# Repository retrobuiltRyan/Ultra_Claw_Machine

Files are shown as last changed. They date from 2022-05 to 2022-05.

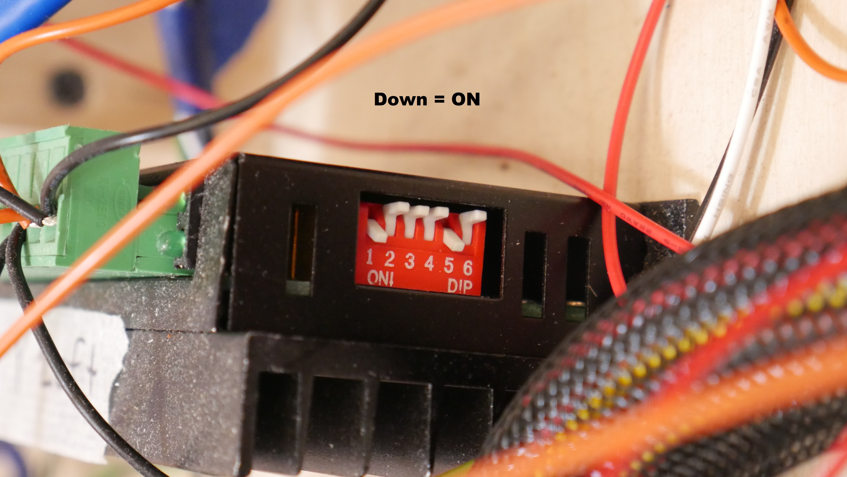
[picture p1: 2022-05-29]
MicroStepping Switch Positions.JPG

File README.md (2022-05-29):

# Ultra_Claw_Machine
A full size (68 x 36 x 31inch) Arduino Mega based claw machine. Borrows most of its design characteristics from DIY CNC machines and 3D printers.
Please watch the Youtube video https://youtu.be/VPqZMdIZ9Dg for a general overview of the design and construction. Happy building!

P1040743
Claw Machn ELECTRICAL Diagram
CAD ariel overview

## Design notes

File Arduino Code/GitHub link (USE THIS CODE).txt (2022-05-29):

https://github.com/LupeCarlos/CMU-TechSpark-Claw-Machine

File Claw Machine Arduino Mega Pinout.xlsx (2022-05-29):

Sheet: Sheet1
CLAW MACHINE PINOUT |  | May 24 2022 | Arduino MEGA
 | OUTPUT | Pin# | Notes
 | X Step (Pul+) | 11
 | X Direction | 10
 | Y1 Step (Pul+) | 9
 | Y1 Direction | 8
 | Y2 Step (Pul+) | 7
 | Y2 Direction | 6 | (mirror of Y1)
 | Z Claw Step (Pul+) | 13
 | Z Claw Direction | 12
 | X Min | 15
 | X Max | 14
 | Y Min | 3
 | Y Max | 2
 | Z Claw Limit | 4
 | LCD i2c | 20 | SDA (cannot be changed)
 | LCD i2c | 21 | SCL (cannot be changed)
 | ClawServo Relay Power | 53
 | Stepper Enable | 52 | Wired to all steppers. LOW = Enable
 | Adressable LED Data | TBD | not implimented yet
 | Claw / Servo PWM | 5
 | INPUT (user controls) | Pin# | Notes
 | Forward (joystick) | 22
 | Backward (joystick) | 23
 | Left (joystick) | 24
 | Right (joystick) | 25
 | Up (button) | 26
 | Down (button) | 27
 | Close (button) | 28
 | Open (button) | 29
 | Start (button) | 30
 | Coin Slot (button) | 31
 | Game Mode (switch) | 16
 | Game Timer Potentiometer | A12
 | Servo Wiring is
 | Orange = GND
 | White = Com
 | Red = +5V

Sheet: ToDo
CLAW MACHINE To Do REV ? |  |  | Arduino MEGA
 | CODE / Electrical | Pin# | Notes
 | Move Motors
 | Mechanical | Pin# | Notes
 | Add master Input Power connector
 | Strain Releif

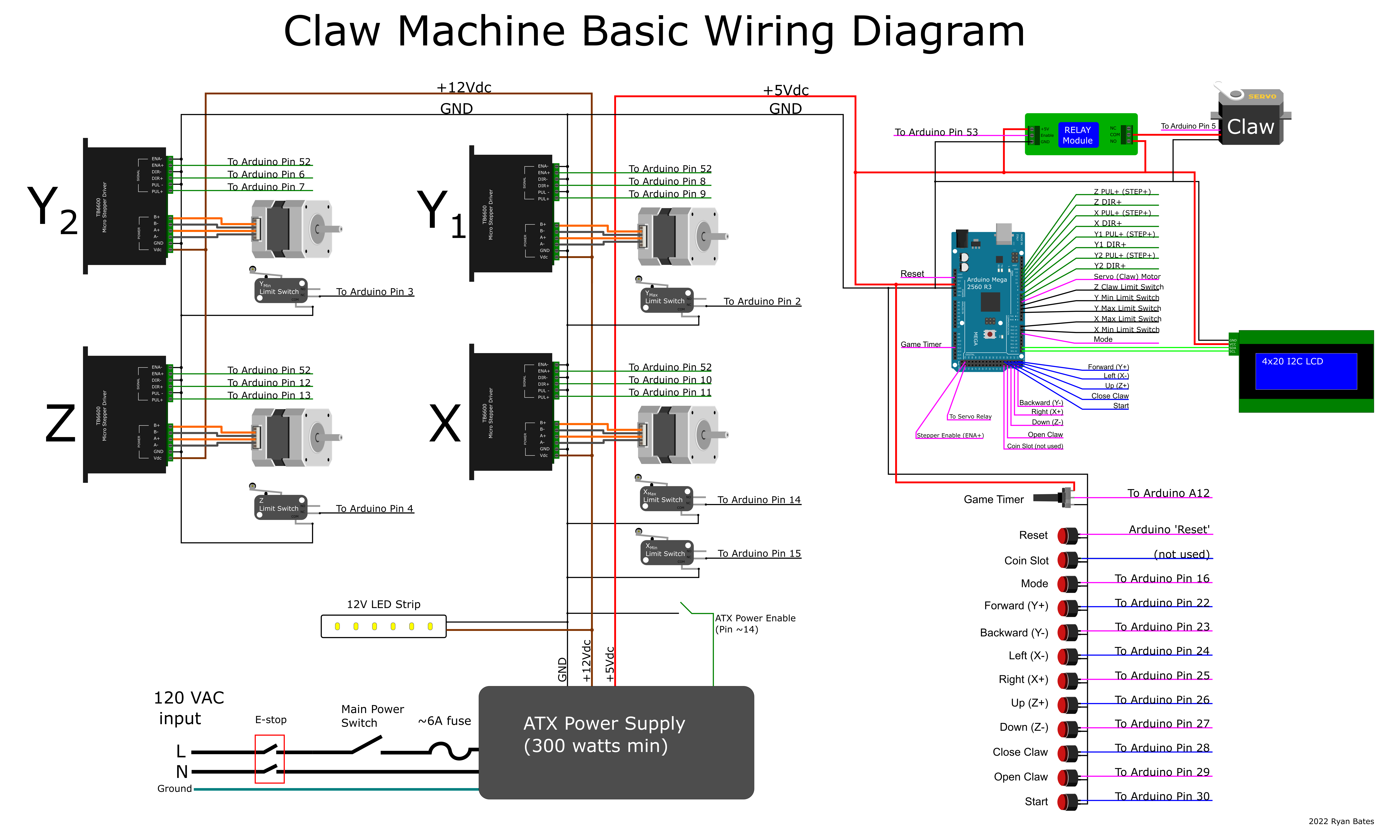
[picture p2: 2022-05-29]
Claw Machn ELECTRICAL Diagram.png

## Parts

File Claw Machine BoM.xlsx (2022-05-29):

Category | Item | Description | Quantity | Cost |  | Line Total
Body | 1 | 3/4 inch Furniture Grade Plywood 8x4 ft sheet | 5 | $73.00 |  | $365.00
 | 2 | Acrylic sheet 0.125in 24x48inch sheet | 3 | $25.00 |  | $75.00
 | 3 | T-molding 3/4inch wide, black (1Ft) | 30 | $0.50 |  | $15.00
 | 4 | Paint + Primer (1 quart each should cover it?) | 1 | $24.00 |  | $24.00
User control | 5 | Arcade Joystick (8-way) | 1 | $16.00 |  | $16.00
 | 6 | Arcade Push Buttons (1.125") | 5 | $2.00 |  | $10.00
 | 7 | Misc Switches, potentiometers, small push buttons | 1 | $7.00 |  | $7.00
Mechanical | 8 | NEMA 23 Stepper Motor | 4 | $30.00 |  | $120.00
 | 9 | Servo Motor | 1 | $10.00 |  | $10.00
 | 10 | Aluminum 1x1 Ft (0.25in thick) 6061 | 2 | $35.00 |  | $70.00
 | 11 | Aluminum Extrusion 1x1inch (3ft section) | 4 | $16.65 | https://www.mcmaster.com/47065T101-47065T412/ | $66.60
 | 12 | Aluminum Extrusion 2x1inch (3ft section) | 1 | $26.00 | https://www.mcmaster.com/47065T107-47065T419/ | $26.00
 | 13 | Aluminum Extrsusion 90degree Brackets | 16 | $7.92 | https://www.mcmaster.com/47065T236/ | $126.72
 | 14 | Hardboard 0.25inch thick 1x1 Ft | 1 | $2.00 |  | $2.00
 | 15 | Cable Carrier | 2 | $18.00 |  | $36.00
 | 16 | lots of misc nut bolt hardware | 1 | $20.00 |  | $20.00
Electrical | 17 | Arduino Mega | 1 | $15.00 |  | $15.00
 | 18 | Arduino Mega Screw Terminal Shield | 1 | $24.00 |  | $24.00
 | 19 | Microswitch | 5 | $1.50 |  | $7.50
 | 20 | Stepper Driver (TB6600) | 4 | $15.00 |  | $60.00
 | 21 | LED lights 12V 1ft White strip | 18 | $2.00 |  | $36.00
 | 22 | Aluminum mounting channel for LED strips, 3m | 1 | $27.00 |  | $27.00
 | 23 | IEC socket with Switch (Fuse Required) | 1 | $4.00 |  | $4.00
 | 24 | Fuse | 1 | $1.00 |  | $1.00
 | 25 | RJ45 Breakout PCB (with RJ45 socket) | 6 | $1.50 |  | $9.00
 | 26 | lots of wires | 99 | $0.25 |  | $24.75
Specialty hardware | 27 | Binding Posts (low profile) Aluminum 8-32 x 0.5inch (pack of 25) | 2 | $16.50 | https://www.mcmaster.com/93121A335/ | $33.00 | black annodized https://www.mcmaster.com/99024A334/
 | 28 | Butteryfly latches | 4 | $3.00 |  | $12.00
 | 29 | Caster wheels if you want to move it | 4 | $6.00 |  | $24.00
 |  |  |  |  |  | $1266.57
 |  | Raw Cost | 1242
 |  | Thrifty build | 567

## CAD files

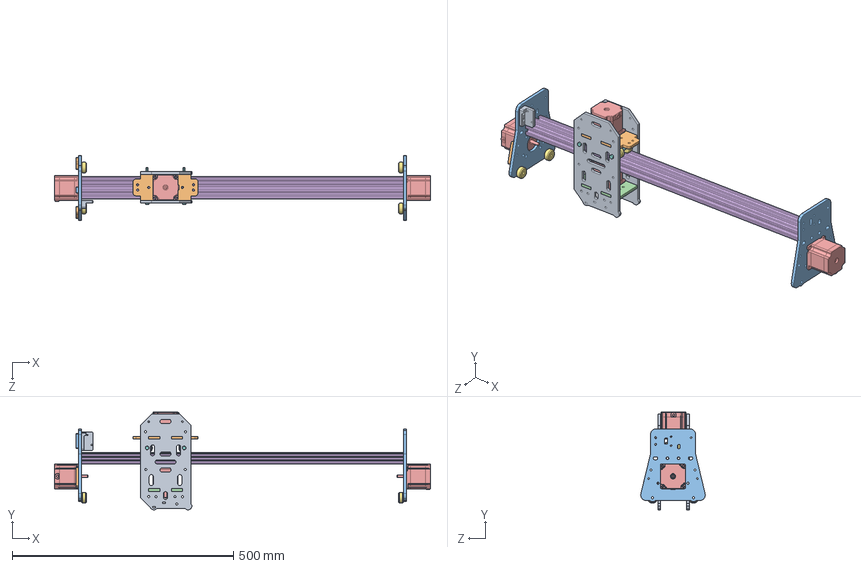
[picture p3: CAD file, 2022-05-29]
Solidworks ClawMachine CAD/Gantry Parts/XYZ Gantry.SLDASM
849.1 x 220.8 x 145.8 mm
Gantry Plate X x 2
Gantry Plate X2
Gantry Plate Y x 2
Gantry Plate Z
Stepper Motor (GrabCAD) x 4
47065T213_T-Slotted Framing
Ilder Wheel x 8
91280A264_Medium-Strength Class 8.8 Steel Hex Head Screw x 2
X Gantry Limit Switch Holder
Y Limit Switch bumper x 2
X Belt Clip

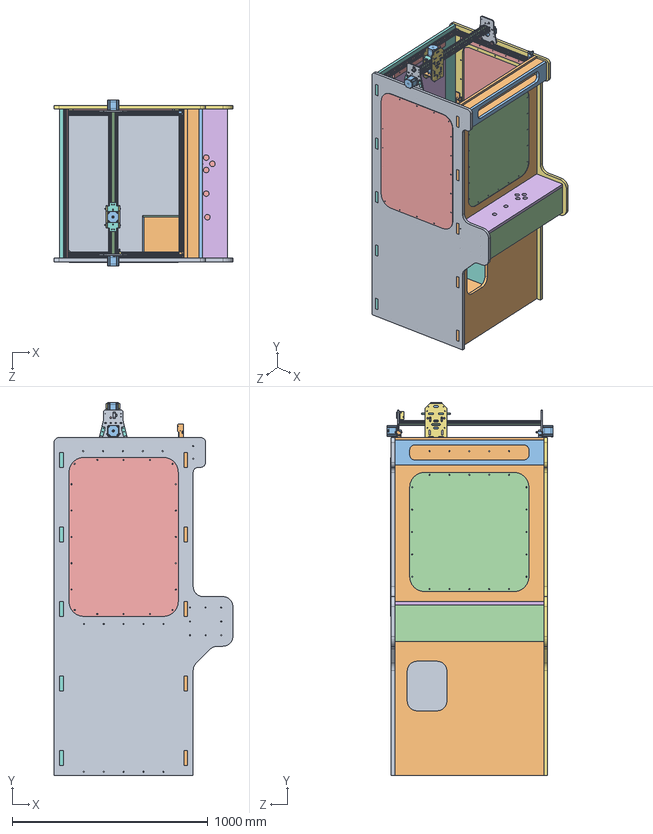
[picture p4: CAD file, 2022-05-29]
Solidworks ClawMachine CAD/Claw Machine.SLDASM
914.4 x 1906.3 x 849.1 mm
Side Panel Body
Front Panel Body
ctrlpanel_side x 2
ctrlpanel_front
ctrlpanel_bottom
ctrlpanel_top
Side Panel Body_right
Back Panel Body
prizefloor
marquee_top x 2
marquee_front
marquee_side x 2
Shelf support bracket 20in x 10
Shelf support bracket 5in
Floor bottom
Prize Chute Right
Prize Chute Rear
Prize Chute Bottom
Prize Floor Barrier A
Prize Floor Barrier B
47065T411_T-Slotted Framing 30in x 2
47065T411_T-Slotted Framing 22.5in x 2
Gantry Plate X x 2
Gantry Plate X2
Gantry Plate Y x 2
Gantry Plate Z
Stepper Motor (GrabCAD) x 4
47065T213_T-Slotted Framing
Ilder Wheel x 8
91280A264_Medium-Strength Class 8.8 Steel Hex Head Screw x 2
X Gantry Limit Switch Holder
Y Limit Switch bumper x 2
X Belt Clip
Y Gantry Limit Switch Holder
Y Gantry Belt Holder
Front Panel Window
Side Panel Window x 2

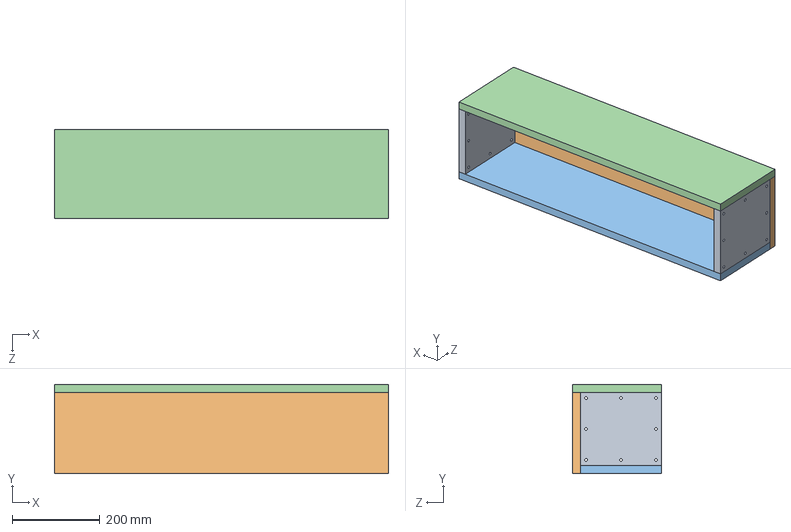
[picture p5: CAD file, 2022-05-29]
Solidworks ClawMachine CAD/ctrlpanel_assem.SLDASM
762.0 x 203.2 x 203.2 mm
ctrlpanel_side x 2
ctrlpanel_front
ctrlpanel_bottom
ctrlpanel_top

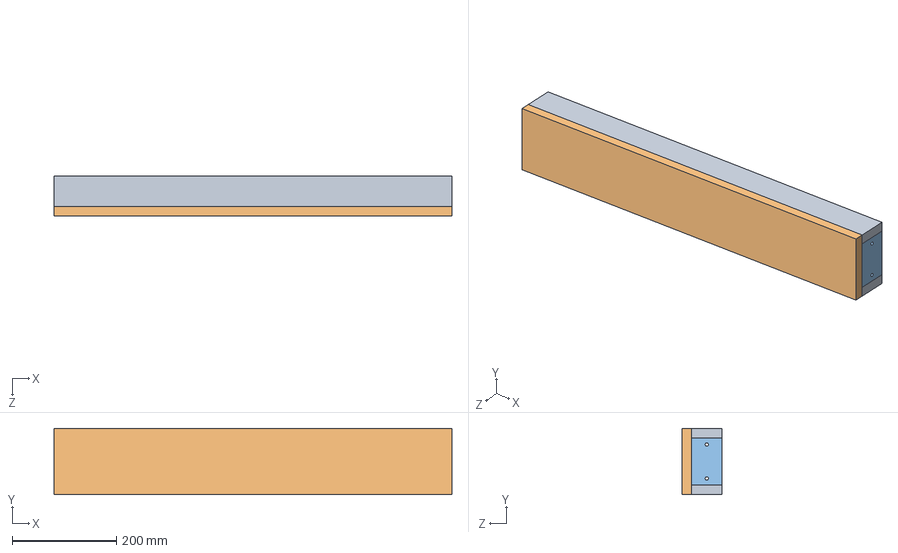
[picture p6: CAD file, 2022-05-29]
Solidworks ClawMachine CAD/marquee_assem.SLDASM
762.0 x 127.0 x 76.2 mm
marquee_top x 2
marquee_front
marquee_side x 2

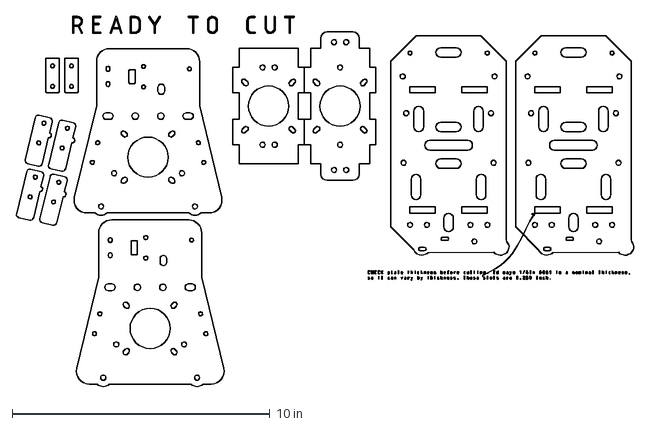
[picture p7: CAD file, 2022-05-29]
Solidworks ClawMachine CAD/Gantry Parts/waterjet claw machine gantry plates.dxf
24.0 x 14.4 in

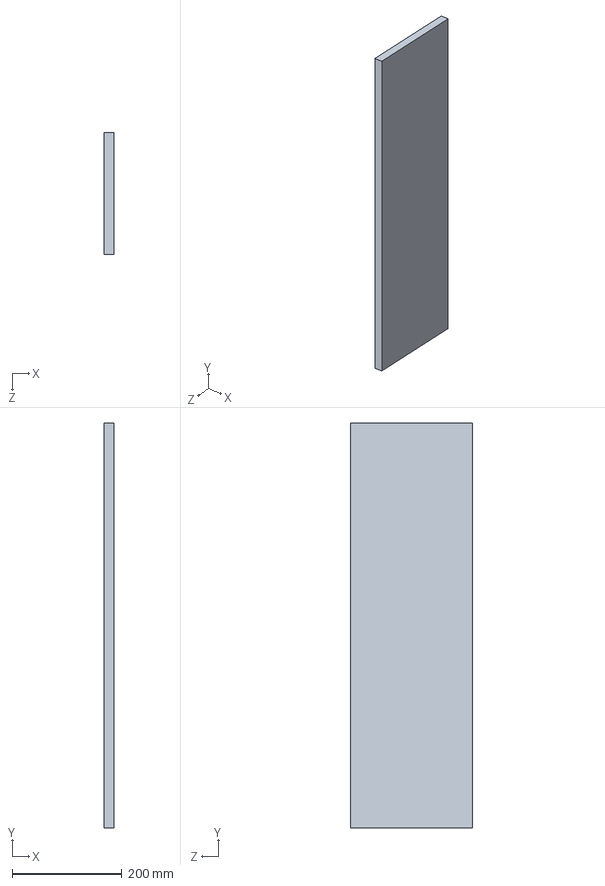
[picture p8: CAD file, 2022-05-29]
Solidworks ClawMachine CAD/Prize Chute Right.SLDPRT
18.3 x 736.6 x 222.2 mm

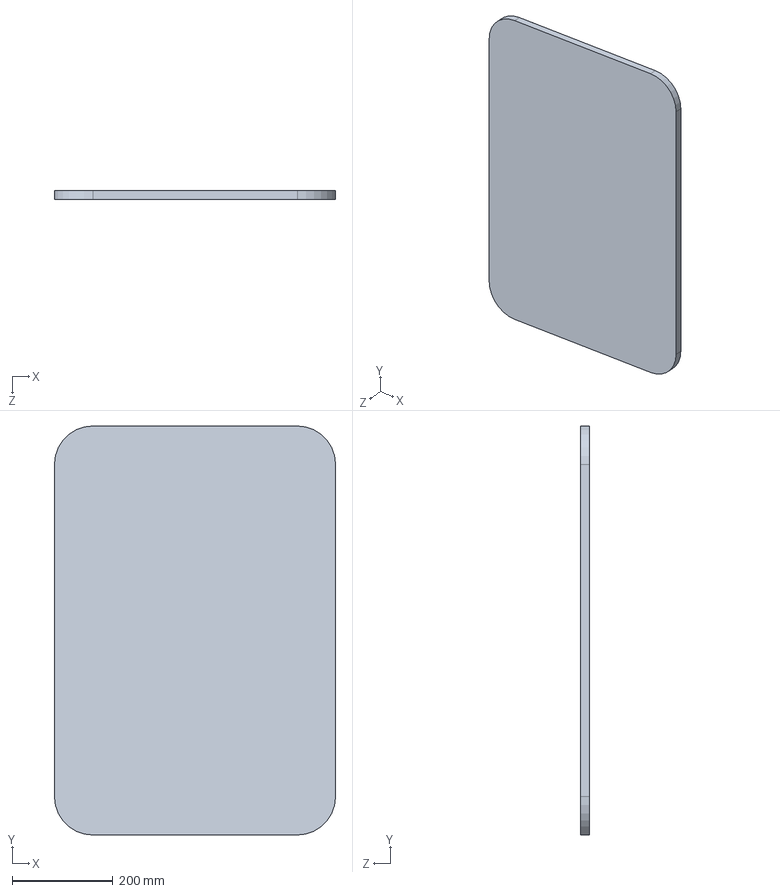
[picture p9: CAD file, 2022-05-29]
Solidworks ClawMachine CAD/Back Panel Removeable Door.SLDPRT
558.8 x 812.8 x 18.3 mm

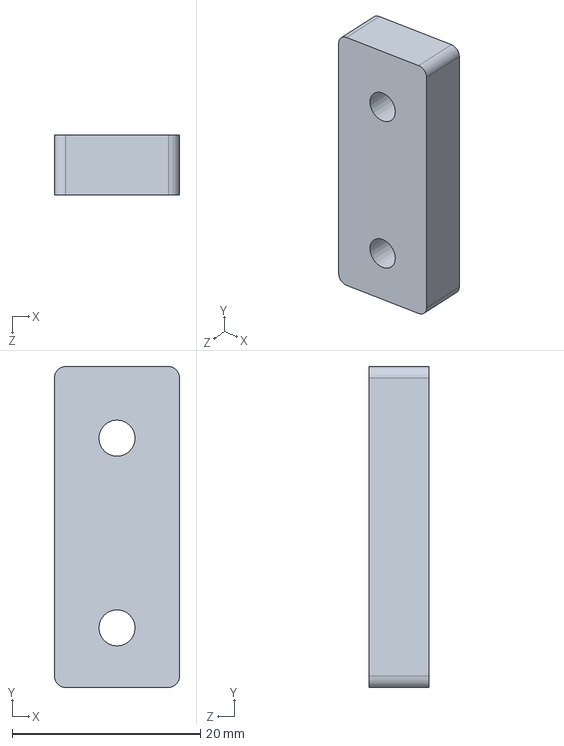
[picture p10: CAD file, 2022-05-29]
Solidworks ClawMachine CAD/Gantry Parts/X Belt Clip.SLDPRT
13.3 x 34.1 x 6.35 mm

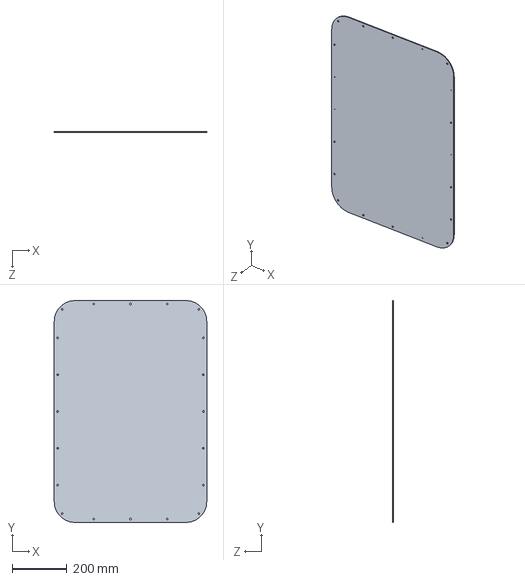
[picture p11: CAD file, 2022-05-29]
Solidworks ClawMachine CAD/Side Panel Window.SLDPRT
558.8 x 812.8 x 3.17 mm

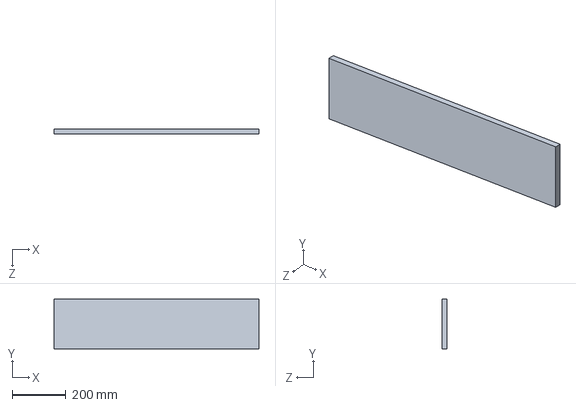
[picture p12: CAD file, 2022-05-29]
Solidworks ClawMachine CAD/ctrlpanel_bottom.SLDPRT
762.0 x 184.9 x 18.3 mm

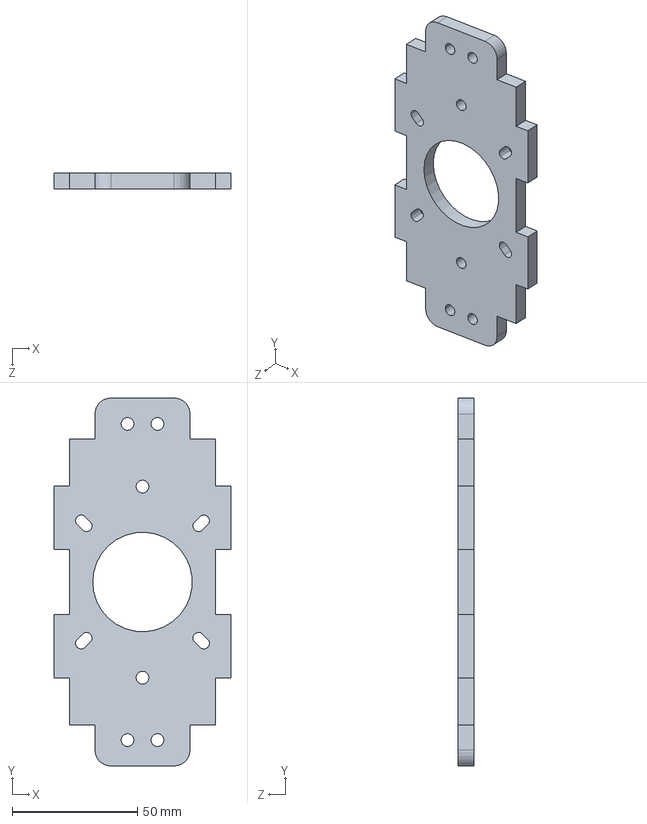
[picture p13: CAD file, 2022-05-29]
Solidworks ClawMachine CAD/Gantry Parts/Gantry Plate X2.SLDPRT
70.5 x 146.7 x 6.35 mm

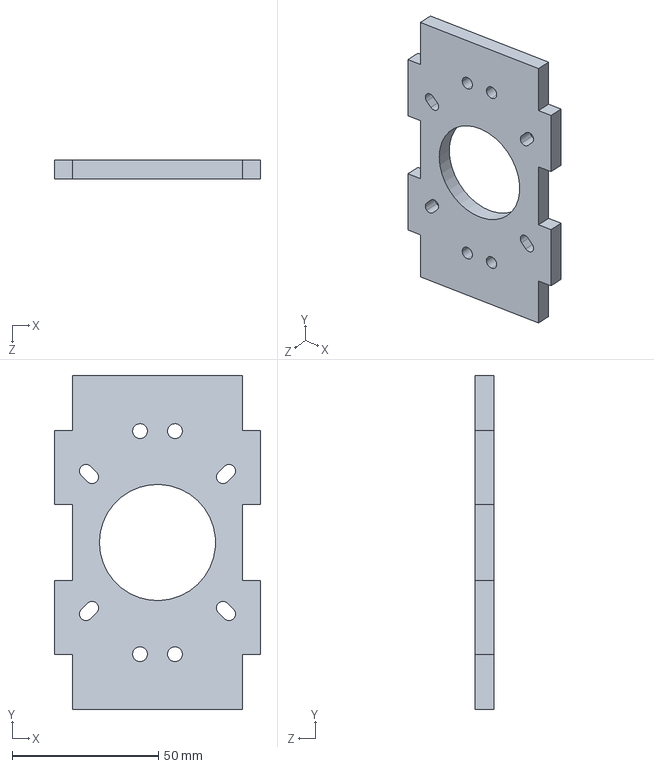
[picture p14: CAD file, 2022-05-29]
Solidworks ClawMachine CAD/Gantry Parts/Gantry Plate Z.SLDPRT
70.5 x 114.1 x 6.35 mm

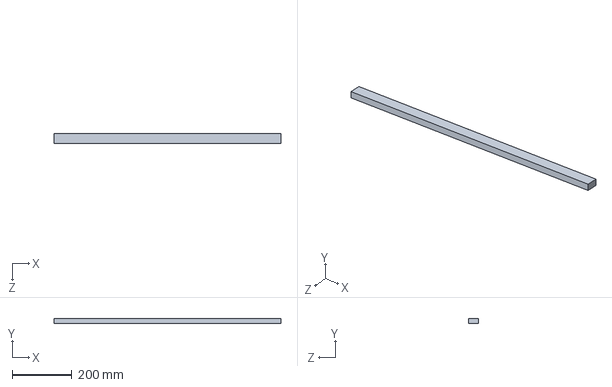
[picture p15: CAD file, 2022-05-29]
Solidworks ClawMachine CAD/marquee_top.SLDPRT
762.0 x 18.3 x 32.5 mm

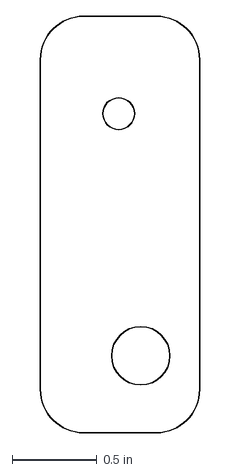
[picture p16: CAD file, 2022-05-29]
Solidworks ClawMachine CAD/bumper for limit switch.dxf
0.942 x 2.46 in

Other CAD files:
Solidworks ClawMachine CAD/Gantry Parts/Ilder Wheel.SLDPRT
Solidworks ClawMachine CAD/Gantry Parts/Y Limit Switch bumper.SLDPRT
Solidworks ClawMachine CAD/RJ45 bracket holder thing.STL
Solidworks ClawMachine CAD/Back Panel Body.SLDPRT
Solidworks ClawMachine CAD/47065T411_T-Slotted Framing 22.5in.SLDPRT
Solidworks ClawMachine CAD/47065T411_T-Slotted Framing 30in.SLDPRT
Solidworks ClawMachine CAD/Back Panel Removable Door.DXF
Solidworks ClawMachine CAD/Floor bottom.SLDPRT
Solidworks ClawMachine CAD/Front Panel Body.SLDPRT
Solidworks ClawMachine CAD/Front Panel Window.DXF
Solidworks ClawMachine CAD/Front Panel Window.SLDPRT
Solidworks ClawMachine CAD/Gantry Parts/47065T213_T-Slotted Framing.SLDPRT
Solidworks ClawMachine CAD/Gantry Parts/91280A264_Medium-Strength Class 8.8 Steel Hex Head Screw.SLDPRT
Solidworks ClawMachine CAD/Gantry Parts/Gantry Plate X.SLDPRT
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

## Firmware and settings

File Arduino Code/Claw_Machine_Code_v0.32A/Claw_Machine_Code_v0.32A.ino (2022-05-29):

// Ryan Bates || Brian Lee
// TechSpark Claw Machine + Accel Stepper Motors
// Sept 29 2021

/* ============Ryan's Change Log [Add new features]:=================
 * Start button, Coin Insert button; triggers game start and game cycles
 * Gameplay loop, 60 second timers 
 * 4x20 i2C LCD to give user feedback and debug
 * [On going] LCD and LED updates are only once per 1 second
 * [On going] Swapped in sub routines to make code more readable
 * [On going] Addressable LEDs change color based on what is happening (idle, in game-timer, gameover)
 * 
 * [Have Not Added] homing functions for  1) power on and 2) gameOver
 * [Have Not Added] Test mode (full control without timer and LCD read what inputs are pressed.)
 * [On going] Serial Monitor debug (print what is happening all the time) will eventually comment out all of this to save processor resources. 
 * [Have Not Added] Demo Mode (press button (secret location) for a random x,y, position and claw grab. 
 * [Have Not Added] Luck/ Mode to toggle between.
 * [Have Not Added] Enable/ Diable Stepper moters & Claw when idle. ENA pin needs to be wired and pulled LOW to cut motor
   power when not in use (Claw Machine is in idle).ENA+ (+5v) ENA- (to arduino) i think this is right? 
 * [Might Change/ Refine] Servo / Claw behavior

i am ass at programming. Sincerely, Ryan
*/
#include <Servo.h>
#include <Stepper.h>
#include <Adafruit_NeoPixel.h> // for addressable RGB LEDs
#define PIN            16 //pin on the Arduino is connected to the NeoPixels?
#define NUMPIXELS      12 // How many NeoPixels are attached to the Arduino?
Adafruit_NeoPixel pixels = Adafruit_NeoPixel(NUMPIXELS, PIN, NEO_GRB + NEO_KHZ800);

#include <Wire.h> 
#include <LiquidCrystal_I2C.h>
LiquidCrystal_I2C lcd(0x27,20,4);  // set the LCD address to 0x27 (address can vary) for a 20 chars and 4 line display

Servo claw;
const int clawPin = 5;
const int clawUp = 26;
const int clawDown = 27;
const int clawClose = 28;
const int clawOpen = 29;
const int startButton = 30;
const int coinInsert= 31; 
const int servoRelay = 53;
const int StepperEnable = 52; /// NEW!
const int stepperSpeedDelay = 1;
const int stepperPulse = 1;

int clawStep = 15; // degrees
int clawCurValue = constrain(clawCurValue, 0, 180);
int clawOpenButtonState = 0;
int clawOpenButtonLastState = 0;
int clawCloseButtonState = 0;
int clawCloseButtonLastState = 0;

const int xStepPin = 11; 
const int xDirPin = 10;
const int y1StepPin = 9;
const int y1DirPin = 8;
const int y2StepPin = 7;
const int y2DirPin = 6;

const int zStepPin = 13;  //(claw up/down)
const int zDirPin = 12;   //(claw up/down)

const int xMinLmtSwtch = 15;
const int xMaxLmtSwtch = 14;
const int yMinLmtSwtch = 3;
const int yMaxLmtSwtch = 2;
const int clawLmtSwtch = 4;

const int forwardJoystick = 22;
const int backwardJoystick = 23;
const int leftJoystick = 24;
const int rightJoystick = 25;

const int stepsPerRevolution = 200;  // change this to fit the number of steps per revolution
//Stepper Xstepper(stepsPerRevolution, 11,11); // library wants 2 or 4 wires (pins) to send pulses too, but these stepper
//Stepper Y1stepper(stepsPerRevolution, 9,9); //  drivers (TB6600?) only step and direction pin to interface. 
//Stepper Y2stepper(stepsPerRevolution, 7,7); //  What i am saying is, this will compile ok, just pay no mind to it. 
//Stepper Zstepper(stepsPerRevolution, 13,13); // 

//------------------time keeping variables for the gameplay loop------------------------------------

//unsigned long previousMillis = 0;            // timestamp made when something happens; dont think this is used anymore.
const long gameloopTimeLimit = 20;             // Game play Time Limit. Time that clawmachine will respond to user input
long elapsedTime;                              // Elasped game time in seconds (counts up!) 
long countDown;                                // Remaining game time in seconds, (counts down!)

unsigned long seconds;
unsigned long gameStartTime;

// ------------------time keeping variables for updating the LCD and LED strips once every so often------------------
unsigned long previousMillis1 = 0;        // will store last time LED was updated
const long updateInterval = 1000;         // interval at which to update user visual feedback

void setup() {
  pinMode(xStepPin, OUTPUT);
  pinMode(xDirPin, OUTPUT);
  pinMode(y1StepPin, OUTPUT);
  pinMode(y1DirPin, OUTPUT);
  pinMode(y2StepPin, OUTPUT);
  pinMode(y2DirPin, OUTPUT);
  pinMode(zStepPin, OUTPUT);
  pinMode(zDirPin, OUTPUT);
  pinMode(servoRelay, OUTPUT);
  pinMode(StepperEnable, OUTPUT);
    
  pinMode(xMinLmtSwtch, INPUT_PULLUP);
  pinMode(xMaxLmtSwtch, INPUT_PULLUP);
  pinMode(yMinLmtSwtch, INPUT_PULLUP);
  pinMode(yMaxLmtSwtch, INPUT_PULLUP);
  pinMode(clawLmtSwtch, INPUT_PULLUP);

  pinMode(clawUp, INPUT_PULLUP);
  pinMode(clawDown, INPUT_PULLUP);
  pinMode(clawOpen, INPUT_PULLUP);
  pinMode(clawClose, INPUT_PULLUP);
  pinMode(forwardJoystick, INPUT_PULLUP);
  pinMode(backwardJoystick, INPUT_PULLUP);
  pinMode(leftJoystick, INPUT_PULLUP);
  pinMode(rightJoystick, INPUT_PULLUP);
  pinMode(startButton, INPUT_PULLUP);


//Xstepper.setSpeed(400);
//Y1stepper.setSpeed(200);
//Y2stepper.setSpeed(200);
//Zstepper.setSpeed(400);
  claw.attach(clawPin); //attaches servo to PWN pin
  pixels.begin();       // This initializes the NeoPixel library.
  
  Serial.begin(9600);   // initialize the serial port:
  
  lcd.init();      //initialize the LCD
  lcd.backlight(); //turn on backlight
  lcd.setCursor(5,0);
  lcd.print("TechSpark's");
  lcd.setCursor(4,1);
  lcd.print("Ultra Claw");
  delay(1000);
  lcd.clear();
}

void loop() {//+++++++++++START OF LOOP+++++++++++++++++++++++++
lcd.setCursor(0,0);
lcd.print("Press Start to play!");
digitalWrite(StepperEnable, HIGH);     // disable motors at the motor driver (EN+)
Serial.println("Press Start to play!");
unsigned long seconds = millis()/1000; // mark the system time as currentmillis
  
  //lcd.setCursor(0,1);   //this is debug, showing the Arduino system time
  //lcd.print("System time: ");lcd.print(seconds); 

  
while (digitalRead(startButton)==LOW){ //enter this loop only when the start button is pressed
      runGameSkill();
  }

 
}  //---------------END OF LOOP---------------------------------



void runGameSkill(){
  lcd.clear();
  digitalWrite(StepperEnable, LOW);     // Enaable motors at the motor driver (EN+)
   digitalWrite(servoRelay, HIGH); // enable power to the servo (claw)
   for(int i=0;i<NUMPIXELS;i++){
    // pixels.Color takes RGB values, from 0,0,0 up to 255,255,255
    pixels.setPixelColor(i, pixels.Color(0,10,0)); // Moderately bright green color.
    pixels.show(); // This sends the updated pixel color to the hardware.
    lcd.setCursor(0,3); lcd.print("elapsed Time: ");
    delay(5); // Delay for a period of time (in milliseconds).
   }
   
  //===========Time Keeping Functions=====MUCH IMPORTANT, NO TOUCH==================================
  gameStartTime = millis()/1000; //mark the system time as 'now'.
while (millis()/1000 - gameStartTime < gameloopTimeLimit){
  elapsedTime = millis()/1000- gameStartTime; // subtract system clock time from the "now" time stamp
  lcd.print(elapsedTime); // using this variable to light LEDs with Game time
  lcd.print("    ");
  LCD_LED_update(); //updates screen and shows some visual feedback for game timer



     
//==================Enable MOVEMENT======================================================
// Movement must be written as while loops. The controls must have program priority so they under inputs feel responsive.
// In the background of each loop time is being checked to force gameover if stuck in movement loop.

  while ((digitalRead(leftJoystick) == LOW) && (digitalRead(xMinLmtSwtch) == HIGH) ){
    countDown = gameStartTime+gameloopTimeLimit-millis()/1000; // this force breaks the loop if the time expires
    if (countDown== 0)
    {break;}
    X_left();  
      LCD_LED_update();  

    }
    
  while ((digitalRead(rightJoystick) == LOW) && (digitalRead(xMaxLmtSwtch) == HIGH)){
    countDown = gameStartTime+gameloopTimeLimit-millis()/1000;
    if (countDown== 0)
    {break;}
   X_right();
     LCD_LED_update();    
   
   }

  while ((digitalRead(forwardJoystick) == LOW) && (digitalRead(yMaxLmtSwtch) == HIGH)) {
    countDown = gameStartTime+gameloopTimeLimit-millis()/1000; // this force breaks the loop if the time expires
    if (countDown== 0)
    {break;}
  Y_forward(); 
    LCD_LED_update();
  
  }
  
  while ((digitalRead(backwardJoystick) == LOW) && (digitalRead(yMinLmtSwtch) == HIGH)){
    countDown = gameStartTime+gameloopTimeLimit-millis()/1000; // this force breaks the loop if the time expires
    if (countDown== 0)
    {break;}
  Y_backward(); 
    LCD_LED_update();
  }

  
  while ((digitalRead(clawUp) == LOW) && (digitalRead(clawLmtSwtch) == HIGH)){
  countDown = gameStartTime+gameloopTimeLimit-millis()/1000; // this force breaks the loop if the time expires
    if (countDown== 0)
    {break;}
  Zclaw_up(); 
    LCD_LED_update(); 
  }

  while ((digitalRead(clawDown) == LOW)){
   countDown = gameStartTime+gameloopTimeLimit-millis()/1000; // this force breaks the loop if the time expires
    if (countDown== 0)
    {break;} 
  Zclaw_down();
    LCD_LED_update();
  }

 clawOpenServo();
 clawCloseServo();

}
gameOver();
returnHome();

}
void LCD_LED_update()                                       {
  unsigned long currentMillis1 = millis();          // does this go here? maybe higher up in the loop
    if (currentMillis1 - previousMillis1 >= updateInterval) {
    // save the last time you updated the status
    previousMillis1 = currentMillis1;
    // do the thing once per interval
     //-----countdown timer and bar animation
     lcd.setCursor(17,1); 
     countDown = gameStartTime+gameloopTimeLimit-millis()/1000; // count down Timer
     lcd.print(countDown); // show the count down seconds so you know the game will end
     if ((gameStartTime+gameloopTimeLimit-millis()/1000) < 10)
     lcd.print(" "); //fixes the missing leading zero for numbers under 10
     lcd.setCursor(4,1); lcd.print("Time Limit:");
     lcd.setCursor((millis()/1000- gameStartTime)*1,2); lcd.write(0xFF); //LCD status bar for time 
     //-----some LED + visual feedback based on how much time is left
    pixels.setPixelColor(countDown, pixels.Color(10,0,0)); //red color.
    pixels.show();
    }}
//void displayTime(){ //obsolete, rolled into the update LED and LCD routine
// //-----countdown timer and bar animation
//     lcd.setCursor(17,1); 
//     countDown = gameStartTime+gameloopTimeLimit-millis()/1000; // count down Timer
//     lcd.print(countDown); // show the count down seconds so you know the game will end
//     if ((gameStartTime+gameloopTimeLimit-millis()/1000) < 10)
//     lcd.print(" "); //fixes the missing leading zero for numbers under 10
//     lcd.setCursor(4,1); lcd.print("Time Limit:");
//     lcd.setCursor((millis()/1000- gameStartTime)*1,2); lcd.write(0xFF); //LCD status bar for time
//  
//}
void returnHome(){
 // code to home machine to prize shoot (x0,y0,z0) 
 // Close claw | wait a second | Goto Z0
 // Lift claw to Z min switch
  while (digitalRead(xMinLmtSwtch) == HIGH)
  X_left();
  while (digitalRead(yMinLmtSwtch) == HIGH)
  Y_forward();
 // Open claw

 // Turn off LEDs
    lcd.clear(); lcd.setCursor(0,0);
    LEDS_off();
}

void gameOver(){
   lcd.clear(); lcd.setCursor(0,0);
    for(int i=0;i<3;i++){ //Blink LEDs on/off red for GAMEOVER
      colorWipe(pixels.Color(0, 0, 0), 0); // Red
      delay(250); // Delay for a period of time (in milliseconds).
      colorWipe(pixels.Color(10, 0, 0), 0); // Red
      delay(250); // Delay for a period of time (in milliseconds).
    }
   lcd.print("GAME OVER!");  // could animate this to stall for time? 
   for (int i=0; i<= 4; i++){
     lcd.print(" GAME OVER!    ");  // could animate this to stall for time? 
     delay(200);            }
   delay(100);
   lcd.clear(); lcd.setCursor(4,1);
    digitalWrite(servoRelay, LOW); //disable power to the servo (claw)
 }
void LEDS_off(){
    for(int i=0;i<NUMPIXELS;i++){ //turn LEDs RED for GAMEOVER
    // pixels.Color takes RGB values, from 0,0,0 up to 255,255,255
    pixels.setPixelColor(i, pixels.Color(0,0,0)); // Turn off.
    pixels.show(); 
    delay(100); // Delay for a period of time (in milliseconds).
    }
}

void colorWipe(uint32_t c, uint8_t wait) {
  for(uint16_t i=0; i<pixels.numPixels(); i++) {
    pixels.setPixelColor(i, c);
    pixels.show();
    delay(0);
  }
}

//==================Gantry Movement subroutines=======Please Keep things tidy=======================
/*
Stepper Xstepper(stepsPerRevolution, 11,11); // library wants 2 or 4 wires (pins) to send pulses too, but these stepper
Stepper Y1stepper(stepsPerRevolution, 7,7); //  drivers TB6600? only step and direction pin to interface. 
Stepper Y2stepper(stepsPerRevolution, 9,9); //  What i am saying is this will compile ok, just pay no mind to it. 
Stepper Zstepper(stepsPerRevolution, 13,13); // 

 */
void X_left(){
  digitalWrite(xDirPin, LOW);   //left direction
  digitalWrite(xStepPin, HIGH); 
  delay(stepperPulse);
  digitalWrite(xStepPin, LOW); 
  delay(stepperPulse);        // speed 
  //Serial.println("Left");
}

void X_right(){
  digitalWrite(xDirPin, HIGH);   //right direction
  digitalWrite(xStepPin, HIGH); 
  delay(stepperPulse);
  digitalWrite(xStepPin, LOW); 
  delay(stepperPulse);        // speed 
 // Xstepper.step(25);
  //Serial.println("Right");
}

void Y_forward(){
  digitalWrite(y1DirPin, HIGH);   //CW
  digitalWrite(y2DirPin, LOW);   //CCW
  digitalWrite(y1StepPin, HIGH); 
  digitalWrite(y2StepPin, HIGH);
  delay(stepperPulse);
  digitalWrite(y1StepPin, LOW); 
  digitalWrite(y2StepPin, LOW);
  delay(stepperPulse);
  //Y2stepper.step(1);
  //Serial.println("Forward");
}

void Y_backward(){
  digitalWrite(y1DirPin, LOW);    //CW
  digitalWrite(y2DirPin, HIGH);   //CCW
  digitalWrite(y1StepPin, HIGH); 
  digitalWrite(y2StepPin, HIGH);
  delay(stepperPulse);
  digitalWrite(y1StepPin, LOW); 
  digitalWrite(y2StepPin, LOW);
  delay(stepperPulse);
  //Serial.println("Backward");
  }

  void Zclaw_up(){
  digitalWrite(zDirPin, HIGH);   //CW
  digitalWrite(zStepPin, HIGH);
  delay(stepperPulse); 
  digitalWrite(zStepPin, LOW);
  delay(stepperPulse); 
  //Zstepper.step(25);
  //Serial.println("up");
  }

  void Zclaw_down(){
  digitalWrite(zDirPin, LOW);   //CCW
  digitalWrite(zStepPin, HIGH);
  delay(stepperPulse); 
  digitalWrite(zStepPin, LOW);
  delay(stepperPulse); 
  //Zstepper.step(25);
  //Serial.println("Down");
  }

  void clawOpenServo(){
 // Claw OPEN
  clawOpenButtonState = digitalRead(clawOpen);
  //Serial.println(clawCurValue);
  // compare the buttonState to its previous state
  if (clawOpenButtonState != clawOpenButtonLastState) 
  {
   
    // if the state has changed, increment the counter
    if (digitalRead(clawOpen)) 
    {clawCurValue = claw.read() + clawStep;
      claw.write(clawCurValue);
      //Serial.println(clawCurValue);
    }
    // Delay a little bit to avoid bouncing
    delay(10);
                                          }
  clawOpenButtonLastState = clawOpenButtonState;
  }
  


  void clawCloseServo(){
  clawCloseButtonState = digitalRead(clawClose);
  // compare the buttonState to its previous statex
  if (clawCloseButtonState != clawCloseButtonLastState) 
  {
   
    // if the state has changed, increment the counter
    if (digitalRead(clawClose)) 
    {clawCurValue = claw.read() - clawStep;
      claw.write(clawCurValue);
      Serial.println(clawCurValue);
    }
    // Delay a little bit to avoid bouncing
    delay(10);
  // save the current state as the last state, for next time through the loop
  clawCloseButtonLastState = clawCloseButtonState;
                            } 
    
  }
